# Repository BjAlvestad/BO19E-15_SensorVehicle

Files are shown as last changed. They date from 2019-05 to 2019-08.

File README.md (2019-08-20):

# BO19E-15 Sensor vehicle for use by students in practical application of interdisciplinary skills 

## Table of Contents

* [About the Project](#about-the-project)
  * [Built With](#built-with)
* [Getting Started](#getting-started)
* [Usage](#usage)
* [Contributing](#contributing)
* [License](#license)
* [Acknowledgements](#acknowledgements)

## About The Project
This project was the bachelor thesis of Bjørnar Alvestad, Benjamin Odland Skare and Erlend Lone.
Our goal was to make a learining tool for automation/electrical engineering students at Western Norway University of Applied Science. The physical car we made has ultrasonic sensors and a LiDAR for measuring distance to obstacles and it has encoders that is used to determine the speed of the car and the distance travelled. HVL SensorVehicle Simulator was made so that the students could test their control logics without having the physical car present.

### Built With
**<u>SensorVehicle-main (UWP app, C#, XAML)</u>**
* Extension that makes it easier to create UWP apps [Windows Template Studio](https://marketplace.visualstudio.com/items?itemName=WASTeamAccount.WindowsTemplateStudio)	

* MVVM framework [Prism](https://prismlibrary.github.io/docs/)

**<u>Simulator-2D</u> (UWP app, C#, XAML)**

* Game developement framework [MonoGame](http://www.monogame.net/)

* Simple 2D camera for Monogame [Comora](https://github.com/aloisdeniel/Comora)

* Map editor [Tiled](https://www.mapeditor.org/)

* Importer for Tiled maps [TiledSharp](https://github.com/marshallward/TiledSharp)

**<u>SensorVehicle-extras (UWP app, C#, XAML, JavaScript, CSS, HTML)</u>**

* Starting point for webcam streaming [HttpWebcamLiveStream](https://github.com/SaschaIoT/HttpWebcamLiveStream/tree/master/HttpWebcamLiveStream)

**<u>Android app for remote control (Java - Android Studio)</u>**

**<u>Code for microcontrollers (C++ - Visual Micro)</u>**

## Getting Started
To fully use HVL SensorVehicle Main and write your own control logic you need to: <br>
* **<u>For writing your own control logic:</u>**
```sh
git clone https://github.com/BjAlvestad/BO19E-15_SensorVehicle-Simplified.git
```
* **<u>For access to the entire software:</u>**
```sh
git clone https://github.com/BjAlvestad/BO19E-15_SensorVehicle.git
```
* Install HVL SensorVehicle Simulator from [Microsoft Store](https://www.microsoft.com/en-us/p/hvl-sensorvehicle-simulator/9nbs6gn8sqlg?activetab=pivot:overviewtab)
* Open SensorVehicle-main.sln and navigate to one of the StudentXX.cs-files

## Usage
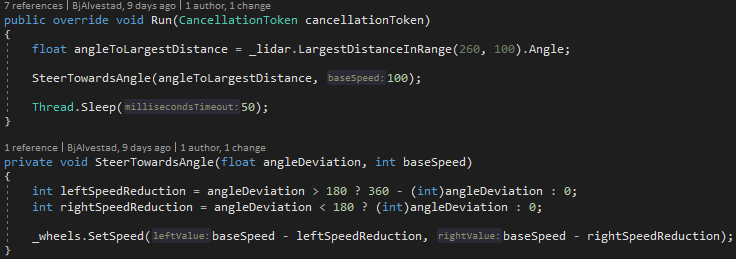
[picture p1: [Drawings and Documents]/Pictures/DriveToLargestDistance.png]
Control logic example
 <br>
The above example shows how one can make the car drive towards the largest distance reported by the LiDAR.

To write your own control logic, navigate to the files in the picture below.
The different StudentXX.cs-files contains instruction where to write the control logic. <br>

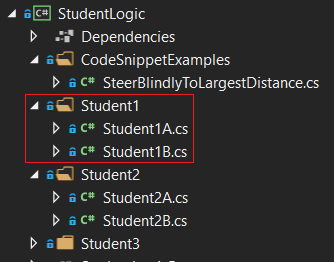
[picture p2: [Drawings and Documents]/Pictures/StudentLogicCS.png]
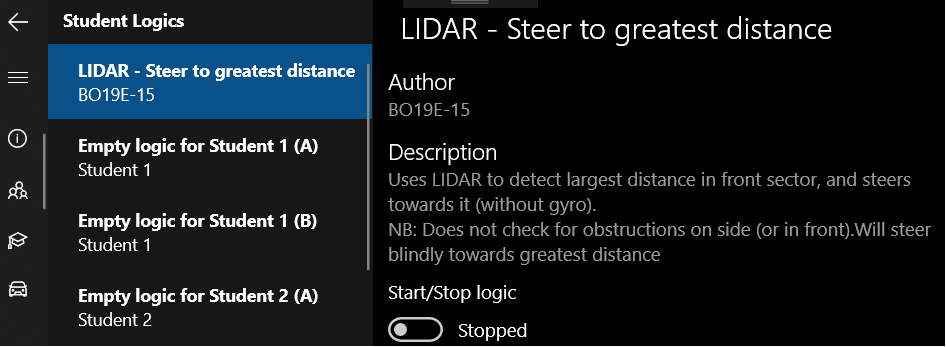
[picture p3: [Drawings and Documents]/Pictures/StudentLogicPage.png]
  <br>
An overview of the different control logics from the shown .cs-files will appear in the student logic page. <br><br>

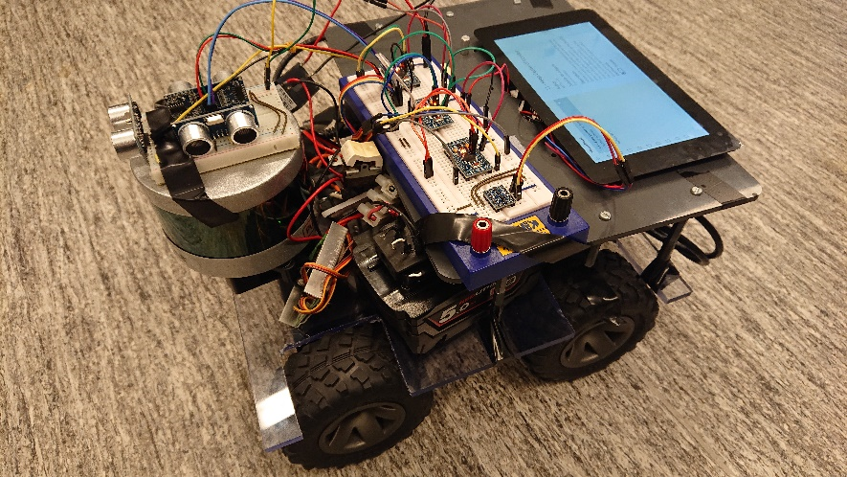
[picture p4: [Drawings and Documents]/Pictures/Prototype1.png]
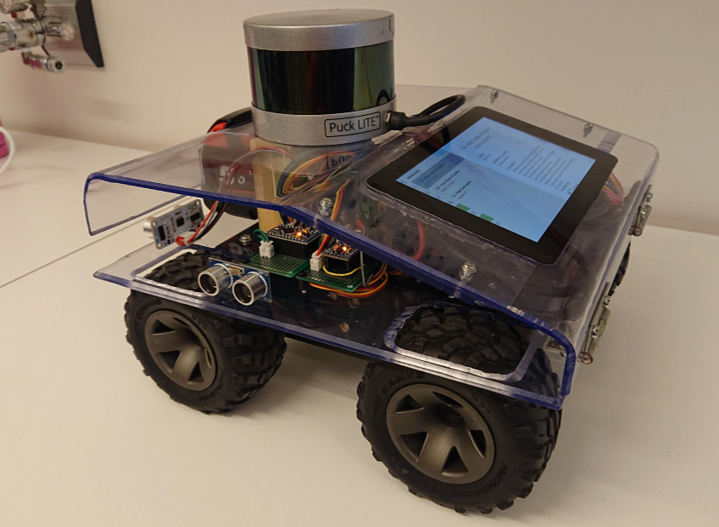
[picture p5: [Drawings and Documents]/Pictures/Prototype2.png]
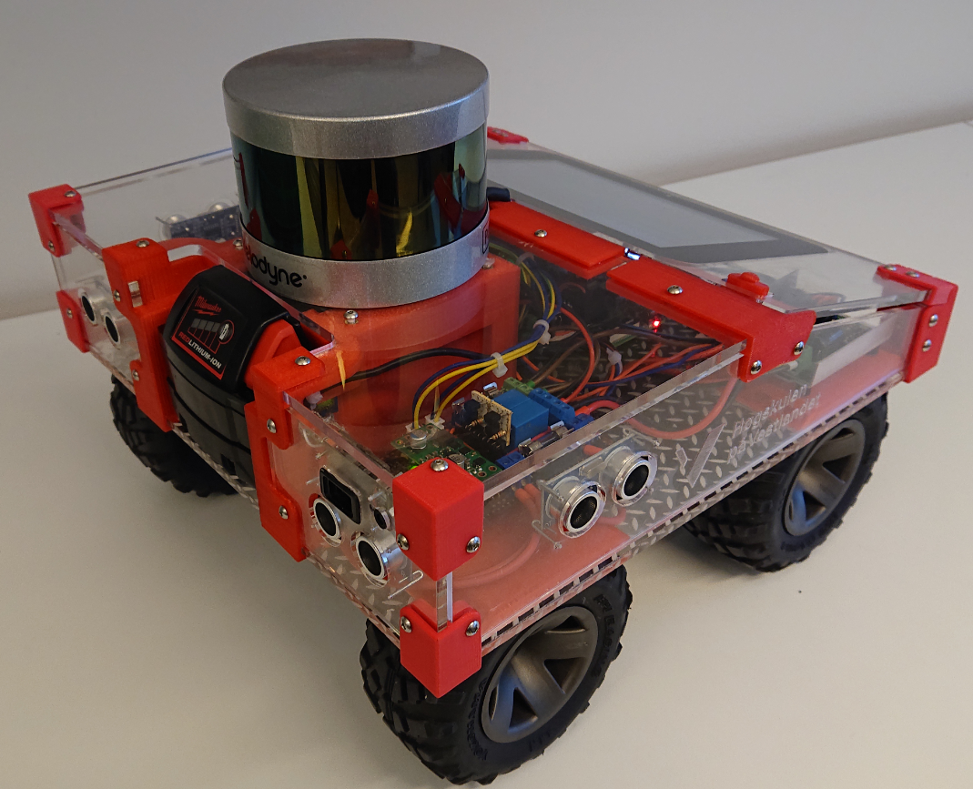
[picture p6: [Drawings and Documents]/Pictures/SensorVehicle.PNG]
         <br><br>
The different version of the car that was made are shown in the pictures above.
The first version was made to get the different hardware components to work.
The second version was made fully functional. The complete software was made by using this version of the sensor vehicle.
The third and final version was made even more solid than the second version. The brackets were 3D-printed and the sheet were cut with laser cutter.

For more information about the development process and a detailed user manual, see [Bachelor thesis document](https://github.com/BjAlvestad/BO19E-15_SensorVehicle/tree/develop/%5BDrawings%20and%20Documents%5D/Bachelor%20Thesis%20(text%20in%20Norwegian)/BO19E-15%20Bacheloropp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) (Norwegian)

## Contributing

Contributions are what make the open source community such an amazing place to be learn, inspire, and create. Any contributions you make are **greatly appreciated**.

1. Fork the Project
2. Create your Feature Branch (`git checkout -b feature/AmazingFeature`)
3. Commit your Changes (`git commit -m 'Add some AmazingFeature`)
4. Push to the Branch (`git push origin feature/AmazingFeature`)
5. Open a Pull Request

## License

Distributed under the MIT License. See `LICENSE` for more information.

## Acknowledgements
* This README is based on [othneildrew's Best-README-Template](https://github.com/othneildrew/Best-README-Template/blob/master/README.md)

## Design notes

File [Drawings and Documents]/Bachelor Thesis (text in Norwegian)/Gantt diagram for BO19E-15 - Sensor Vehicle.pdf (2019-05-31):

12 | 17 | 24 | 31 | 7 | 14 | 21 | 28 | 4 | 11 | 18 | 25 | 4 | 11 | 18 | 25 | 1 | 8 | 15 | 22 | 29 | 6 | 13 | 20 | 27 | 3 | 10
| | Dec '18 | | | Jan '19 | | | | | Feb '19 | | | | Mar '19 | | | | Apr '19 | | | | | May '19 | | | Jun '19
BO19E-15 - Sensor Vehicle ... | 0h | 58%
Møter, presentasjoner og innleveri... | 0h | 63%
Innlevering av forstudie | 0 | 100%
Midtveispresentasjon | 0 | 100%
Bacheloroppgave seminar | 0 | 100%
Innlevering av bacheloroppgave | 0 | 0%
Presentasjon av bacheloroppgave | 0 | 0%
EXPO / avslutningsfest | 0 | 0%
Presentasjon for forkursstudenter | 0 | 100%
Bacheloroppgaveseminar | 0 | 100%
Documentation & Reports | 0h | 23%
Forstudie | 0 | 100%
Brukermanual | 0 | 0%
Bacheloroppgave | 0 | 0%
(hvis tid) Kodeforklaring | 0 | 0%
Hardware & Microcontrollers | 0h | 100%
Analog styring av hjul | 0 | 100%
Avstandsmåling med ultrayd | 0 | 100%
Touch skjerm | 0 | 100%
Power distributer | 0 | 100%
Sensor Vehicle base functions compl... | 0 | 100%
Collision protection | 0 | 90%
(if time) Look into possibility for addi... | 0 | 0%
Main UWP app | 0h | 52%
Sensor input - LIDAR | 0 | 100%
Sensor input - Ultralyd | 0 | 100%
Distance klasse (autoselect from LID... | 0 | 0%
Vehicle control - Klasse for å sette hj... | 0 | 100%
Interface for Eksempel/Student logikk | 0 | 90%
Launch simulator if running on PC | 0 | 100%
AppService Client | 0 | 100%
Improve robustness / code cleanup | 0 | 0%
Rewrite code to Async | 0 | 0%
Simulator | 0h | 72%
Prework on simulator | 0 | 100%
Write or find TiledMap importer/pars... | 0 | 100%
Create class for simulating LIDAR | 0 | 100%
Configure as AppService provider | 0 | 100%
Send LIDAR distance to / receive spe... | 0 | 100%
TEST simulator physics against real ... | 0 | 100%
(if time) Give option to select maps | 0 | 0%
(if time) Create more maps | 0 | 0%
Extras - Streaming | 0h | 89%
Prework on streaming app | 0 | 100%
Add streaming possibility | 0 | 100%
Add layout of UWP app | 0 | 100%
Keep streaming when app is in backg... | 0 | 100%
Add functionality from IoT Dashboard | 0 | 100%
Add possibility to launch main app | 0 | 100%
Remove unused/unnecessary code | 0 | 100%
Finish what is marked TODO in code | 0 | 0%
Extras - Android | 0h | 0%
Example Control Logic / Student ta... | 0h | 0%
Eks. Logikk 01 - Hold midten av kori... | 0 | 100%
Eks. Logikk 02 - Right hand search w/... | 0 | 0%
(if time) Eks. Logikk 03 - Build map | 0 | 0%

Erlend Lone
Benjamin Skare, Bjørnar Alvestad, Erlend Lone Benjamin Skare, Bjørnar Alvestad, Erlend Lone Erlend Lone
Benjamin Skare, Bjørnar Alvestad, Erlend Lone Benjamin Skare, Bjørnar Alvestad, Erlend Lone Benjamin Skare, Bjørnar Alvestad, Erlend Lone Benjamin Skare, Bjørnar Alvestad, Erlend Lone

Benjamin Skare
Benjamin Skare, Erlend Lone Benjamin Skare
Benjamin Skare
Benjamin Skare, Erlend Lone

Bjørnar Alvestad

Bjørnar Alvestad
Bjørnar Alvestad

Bjørnar Alvestad

Bjørnar Alvestad
Bjørnar Alvestad, Erlend Lone Bjørnar Alvestad
Bjørnar Alvestad
Bjørnar Alvestad
Erlend Lone

Erlend Lone

Erlend Lone
Erlend Lone
Erlend Lone
Erlend Lone
Erlend Lone
Erlend Lone
Erlend Lone
Erlend Lone

Powered by TCPDF (www.tcpdf.org)

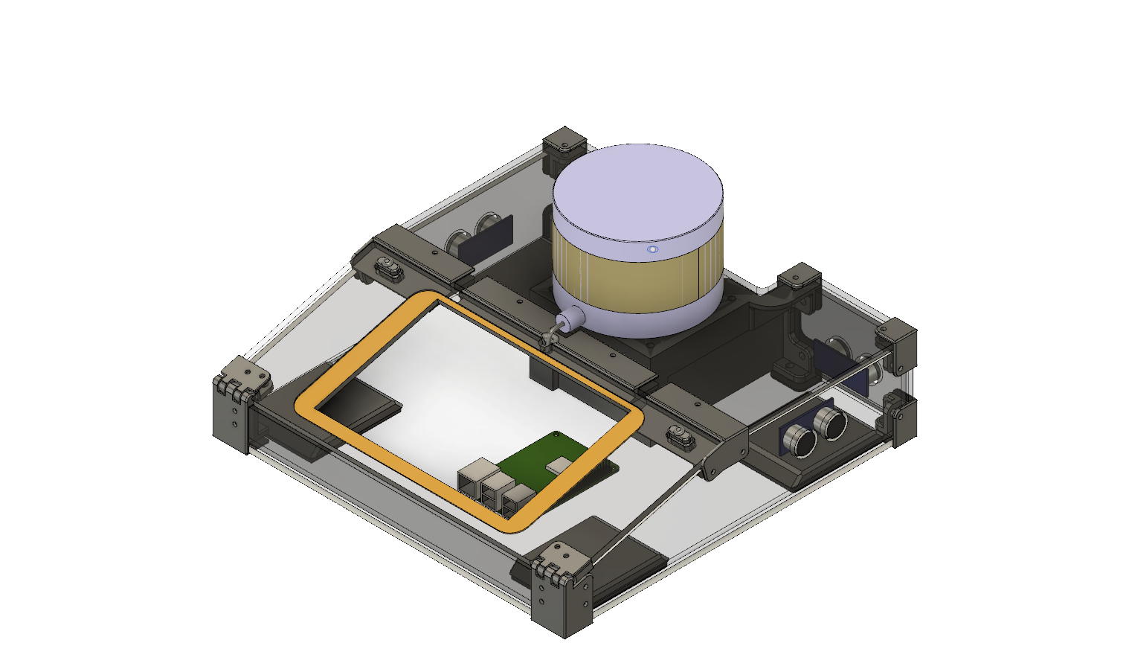
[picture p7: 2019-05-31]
[Drawings and Documents]/Hardware design and components/3D models of vehicle chassis/Chassi v41.1 - Aft right.png

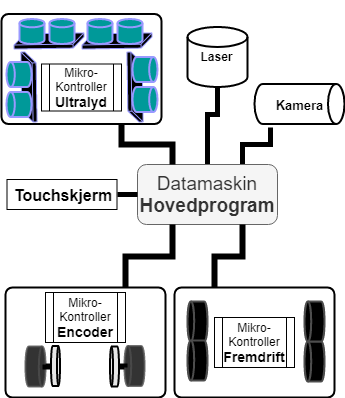
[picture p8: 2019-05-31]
[Drawings and Documents]/System and application drawings/Simplified system schematics (text in Norwegian).png

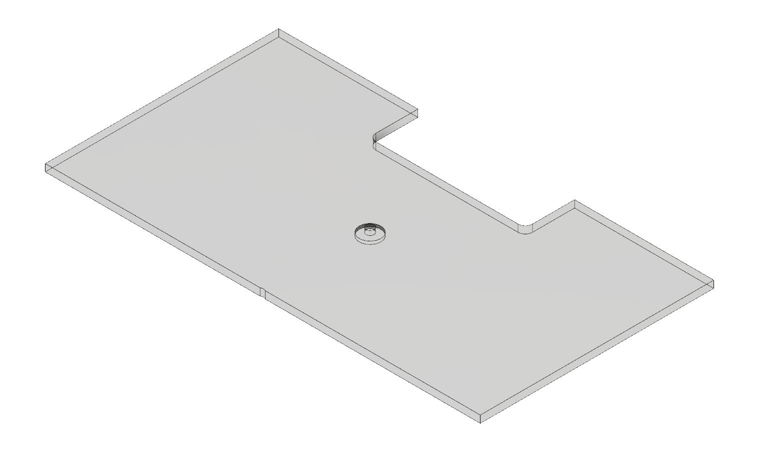
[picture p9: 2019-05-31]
[Drawings and Documents]/Hardware design and components/3D models of vehicle chassis/Plates/Topp v18.png

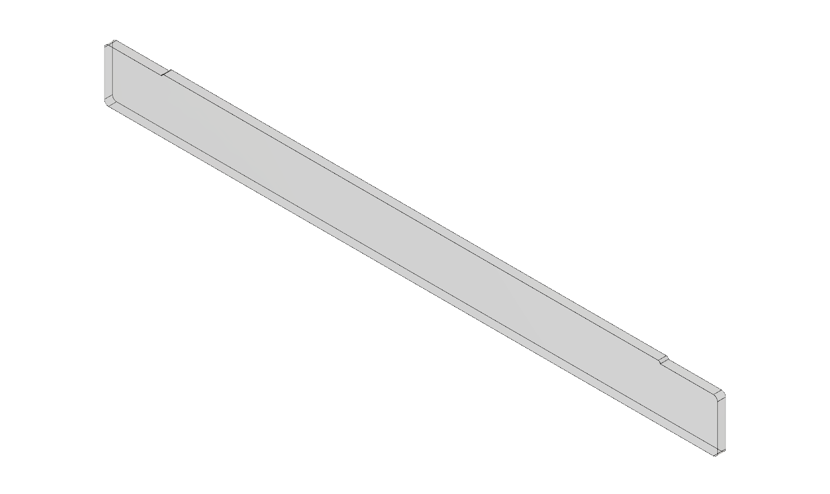
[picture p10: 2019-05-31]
[Drawings and Documents]/Hardware design and components/3D models of vehicle chassis/Plates/Bak v17.png

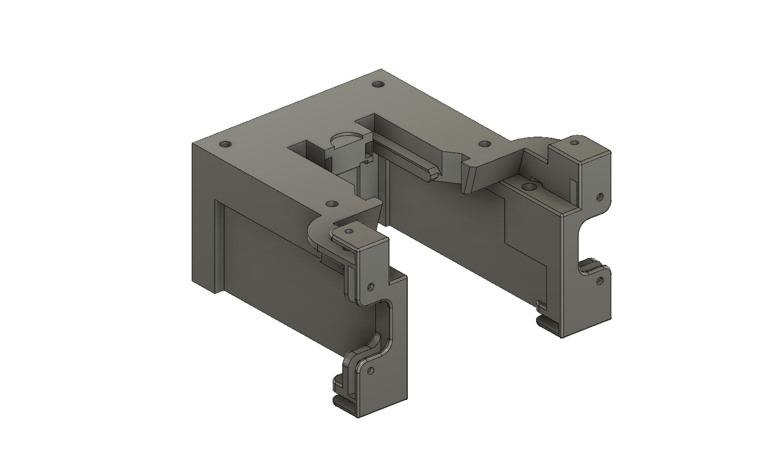
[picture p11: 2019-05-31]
[Drawings and Documents]/Hardware design and components/3D models of vehicle chassis/Brackets/Batteriholder3 v33.png

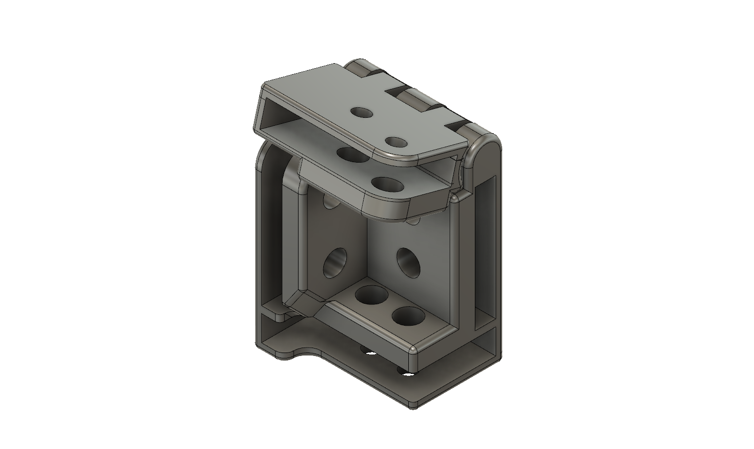
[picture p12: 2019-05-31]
[Drawings and Documents]/Hardware design and components/3D models of vehicle chassis/Brackets/Brakett BV v45.png

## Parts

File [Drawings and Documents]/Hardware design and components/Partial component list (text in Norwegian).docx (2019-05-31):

###### A.1 Komponentliste

###### A.1.1 Ettkortsdatamaskin

7" universal LCD | m/touch
HDMI kabel | HMDI til mini-HDMI
USB kabel | Mini til type A
Raspberry Pi 3B
Kjøleribber | m/vifte
DC-regulator | 5 til 3,3 volt
Logic level coverter | I2C
Koblingspunkt

###### A.1.2 Sensorer og moduler

Motordriver | Sabertooth 2X12 RC
Ultrasonic sensor | HC-SR04 | 4 stk
Velodyne Lidar VLP-16 | m/koblingsboks, bolt(tomme)
Nettverkskabel | Cat 5, RJ-45
Webkamera | Microsoft LifeCam HD-3000
Batteri m/lader | Milwaukee M18™ 5.0 AH | 2 stk
DC-motor m/gir | (2 stk med enkoder) | 4 stk
Gyro | Bosch BNO055 9-Axis IMU | 2 stk (ikke på bil)
Gyro | MPU 9250 SPI/IIC 9-Axis | 2 stk (ikke på bil)

###### A.1.3 Strømstyring til Arduino og RPI:

NPN transistor | 2N3906
PNP transistor | 2N3904
Motstand | 100 k ohm
Motstand | 10 k ohm | 2 stk
Koblingspinner

###### A.1.4 «Arduino-kort»:

Arduino Pro-Mini | ATmega328P | 4 stk
I2C buffer IC | TCA4311A | 4 stk
Motstand | 100 k ohm
Motstand | 10 k ohm
Mikrobryter | | 2 stk
Lysdioder
Kontakter
Kretskort
Koblingspunkt

###### A.1.5 Strømforsyning:

Rele | | 4 stk
Sikring | | 4 stk
Sikring
Sikring
5 VDC regulator
Kontakter
Kretskort
Koblingspunkt

###### A.1.6 Festemidler og resten:

Skruer Hex | | 4 stk
Skruer nedsenket | | 4 stk
Avstandsstykker | Plast m/skruer
Gjenger
Plexiglass
Plast
Lydisolasjonsmatte
Ledning
Niter
Ledninger
Kontakter
Strips
Superlim
Stifter dykkert

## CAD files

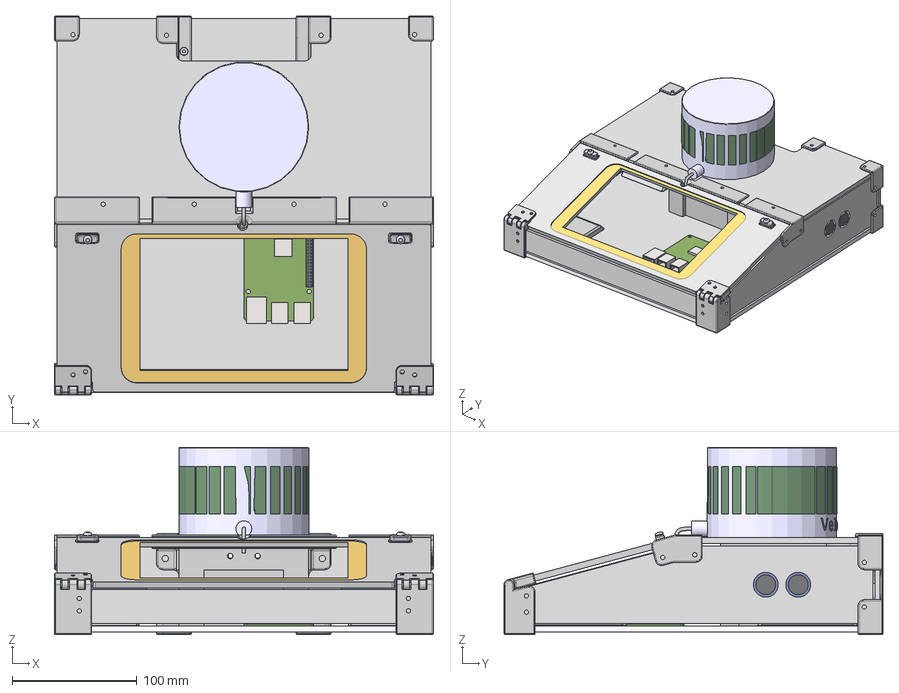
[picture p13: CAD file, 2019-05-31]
[Drawings and Documents]/Hardware design and components/3D models of vehicle chassis/Chassi v41.step
304.3 x 304.0 x 150.1 mm
Bunnplate
Brakett FV x 2
Brakett FV v4(Mirror) x 2
Topp
Side x 2
hjulskjerm x 4
Batteriholder3
Velodyne2
Raspi3B+_Mock
Skjemplate
Bak
SkjermFeste
Ultrasonic x 4
Kamera
Bryter
Component3(Mirror)
Component4(Mirror)

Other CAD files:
[Drawings and Documents]/Hardware design and components/3D models of vehicle chassis/Brackets/Batteriholder3 v33.f3d
[Drawings and Documents]/Hardware design and components/3D models of vehicle chassis/Brackets/Brakett BV v45.f3d
[Drawings and Documents]/Hardware design and components/3D models of vehicle chassis/Brackets/Brakett FV v8.f3d
[Drawings and Documents]/Hardware design and components/3D models of vehicle chassis/Brackets/SkjermFeste v22.f3d
[Drawings and Documents]/Hardware design and components/3D models of vehicle chassis/Brackets/hjulskjerm v9.f3d
[Drawings and Documents]/Hardware design and components/3D models of vehicle chassis/Components/Bryter v2.f3d
[Drawings and Documents]/Hardware design and components/3D models of vehicle chassis/Components/Kamera v2.f3d
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

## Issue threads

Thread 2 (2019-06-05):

Standardise all sensors to report distances in meters (encoder is currently in cm)

BjAlvestad, 2019-06-05:
In the main program, the public properties in Encoder classes exposes distance values as centimeters, while the other sensors utilizes meters.
This may cause confustion for the people writing control logics for the vehicle.

Two alternative options that would fix the issue:

**Option 1**:
- Add aditional metod reporting distance in meters (in addition to cm).
This would mean an increment of the minor version (new functionality but no breaking change).

**Option 2**
- Change methods in main program to utilize values as meters instead of centimeters.
- Modify the Encoder page and overview page to also reflect these changes (the displayed units).
This would mean an increment of the major version (breaking change for code allready using data from the encoders).

PS:
The microcontroller should still transfere the distance as centimeters and a whole number.
The change should only be carried out in the main program (dividing the received distance by 100).

PPS:
The versioning refered to above in the two options is based on [Semantic Versioning 2.0.0](https://semver.org/)

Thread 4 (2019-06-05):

Rewrite code to utlilize async/await fully in the SensorVehicle-main app (requires async I2c library) - responsive UI

BjAlvestad, 2019-06-05:
There is a mix of async and synchronous code in the SensorVehicle-main application.
Async/await should be used "from bottom to top".

When the code is running on a PC (against the simulator), the implementation for IVehichleCommunication that is used is "SimulatedVehicleCommunication". This utilizes an AppService to communicate with the simulator, which only offers async methods.

When the code is running on the physical car, the implementation for IVehicleCommunication is "VehicleCommunication" which utilizes the UWP I2c library. This offers only synchronous methods. Async is not an option here.

For this reason, we have been forced to mix async and non-async code.

### The way we have solved this:
Inside "SimulatedVehicleCommunication"-class:

**When sending data to simulator** (setting wheel speed) we send without awaiting the task.
Problem caused by this: any exceptions that occurs behind this method will be swallowed since we are not awaiting them.

**When requesting data from simulator** we force the method to run synchronously by adding ".GetAwaiter().GetResult();" to the async method.
Potential problem: may cause code to deadlock, however this has not occured while we have been testing the code.

### Better way of fixing issue - if async I2C library can be found
If Microsoft releases an async version of the I2C library, then it would be better to rewrite all the code to async, since this would also ensure that the GUI remains responsive.
(If I2c communication fails there will be approximately a seconds delay before an exception is thrown. If the update was initiated from the GUI, this will cause a momentary UI freeze).

PS: This suggestion for fix is only relevant if an async I2c library can be found.

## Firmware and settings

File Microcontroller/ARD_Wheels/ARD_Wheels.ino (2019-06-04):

// Code for SensorVehicle v.1.0
// BO19E-15


// Communication
#include <Wire.h>
const int pin_I2C_enable = 14;
const int address = 0x20;
const int size_of_byte_array = 23;
void receive_event(int x);
void assemble_ints_from_byte_array(long number_of_longs, int start_index, byte array[]);
void assemble_data_from_vehicle(byte vehicle_byte_array[]);

// PWM
#include <Servo.h>
Servo wheels_right;
Servo wheels_left;

const int pin_pwm_right = 7;
const int pin_pwm_left = 6;
const int pin_mode_1 = 11;
const int pin_mode_2 = 10;
const int pin_relay_sabertooth = 9;
const int pin_mode_switch = 12;

const int data_standstill = 0;
const int data_full_reverse = -100;
const int data_full_forward = 100;
const int pwm_start_reverse = 1330;
const int pwm_full_reverse = 1130; // 12 v (1000)
const int pwm_start_forward = 1600;
const int pwm_full_forward = 1840;  // 12 v (2000)
const int pwm_standstill = 1500;
const int ramp_up = 20;

int data_left, data_right;
int speed_left, speed_right;
int speed_map(int data);

// Safety mode
int mode = 2;  // 3 = full speed, 0 = stop
int data_check(int data);
int mode_check(int data);

void setup()
{
	Wire.begin(address);

	pinMode(pin_mode_1, INPUT_PULLUP);
	pinMode(pin_mode_2, INPUT_PULLUP);
	pinMode(pin_relay_sabertooth, OUTPUT);
	pinMode(pin_mode_switch, INPUT_PULLUP);
	pinMode(LED_BUILTIN, OUTPUT);

	digitalWrite(pin_relay_sabertooth, LOW);

	wheels_right.attach(pin_pwm_right);
	wheels_left.attach(pin_pwm_left);
	wheels_left.writeMicroseconds(pwm_standstill);
	wheels_right.writeMicroseconds(pwm_standstill);
	Wire.onReceive(receive_event);

	data_left = data_standstill;
	data_right = data_standstill;
	speed_left = pwm_standstill;
	speed_right = pwm_standstill;

	pinMode(pin_I2C_enable, OUTPUT);
	digitalWrite(pin_I2C_enable, HIGH);
}

void loop()
{
	if (data_left==0 && data_right == 0)
	{
		digitalWrite(pin_relay_sabertooth, LOW);
	}
	else
	{
		digitalWrite(pin_relay_sabertooth, HIGH);
	}

	speed_left = speed_map(mode_check(data_left));
	speed_right = speed_map(mode_check(data_right));
	
	wheels_right.writeMicroseconds(speed_right);
	wheels_left.writeMicroseconds(speed_left);

	/*String s = "Ld: = " + String(data_left) + "\t Rd: " + String(data_right) +
		"\t L: " + String(speed_left) + "\t R: " + String(speed_right) +
		"\t MODE: " + mode +
		"\t SWITCH: " + digitalRead(pin_mode_switch);
	Serial.println(s);
	delay(1000);*/
}

void receive_event(int x)
{
	byte data[size_of_byte_array];
	
	if (Wire.available())
	{
		for (int i = 0; i < size_of_byte_array; i++)
		{
			data[i] = Wire.read();
		}
		assemble_data_from_vehicle(data);
	}
}

int speed_map(int data)
{
	if (data > 0)
	{
		data = map(data, data_standstill, data_full_forward, pwm_start_forward, pwm_full_forward);
		return data;
	}
	else if (data < 0)
	{
		data = map(data, data_standstill, data_full_reverse, pwm_start_reverse, pwm_full_reverse);
		return data;
	}
	else
	{
		return pwm_standstill;
	}
}

int data_check(const int data)
{
	if (data < data_full_reverse)
	{
		return  data_full_reverse;
	}
	else if (data > data_full_forward)
	{
		return data_full_forward;
	}
	else
	{
		return data;
	}
}

int mode_check(int data)
{
	if (digitalRead(pin_mode_switch))
	{
		digitalWrite(LED_BUILTIN, HIGH);
		mode = 2;
		return (2 * data) / 3;
	}
	digitalWrite(LED_BUILTIN, LOW);

	if (!digitalRead(pin_mode_1) && !digitalRead(pin_mode_2) )
	{
		mode = 0;
		return 0;
	}
	else if (!digitalRead(pin_mode_1) && digitalRead(pin_mode_2))
	{
		mode = 1;
		data = data / 2;
		return data;
	}
	else if (digitalRead(pin_mode_1) && !digitalRead(pin_mode_2))
	{
		mode = 2;
		data = (2 * data) / 3 ;
		return data;
	}
	else if (digitalRead(pin_mode_1) && digitalRead(pin_mode_2))
	{
		mode = 3;
		return data;
	}
	return 0;
}

void assemble_data_from_vehicle(byte vehicle_byte_array[])
{
	int address = vehicle_byte_array[0];
	int code = vehicle_byte_array[1];
	const int number_of_longs = vehicle_byte_array[2];
	const int empty_bytes = 3;
	assemble_ints_from_byte_array(number_of_longs, empty_bytes, vehicle_byte_array);
}

void assemble_ints_from_byte_array(const long number_of_longs, const int start_index, byte array[])
{
	if (size_of_byte_array >= (sizeof(long)*number_of_longs + start_index))
	{
		const int bits_in_long = sizeof(long) * 8;
		long longs[2];

		for (int i = 0; i < number_of_longs; i++)
		{
			int assembled_long = 0;
			const int shift_by_long = sizeof(long) * i;

			for (int j = 1; j <= sizeof(long); j++)
			{
				assembled_long |= array[start_index - 1 + j + shift_by_long] << (bits_in_long - 8 * j);
			}
			longs[i] = assembled_long;
		}

		data_left = data_check(longs[0]);  // Between -100 and 100;
		data_right = data_check(longs[1]);
	}
}

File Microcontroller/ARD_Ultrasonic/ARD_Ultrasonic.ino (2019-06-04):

// Code for SensorVehicle v.1.0
// BO19E-15

// https://create.arduino.cc/projecthub/MisterBotBreak/how-to-use-an-ultrasonic-sensor-181cee

// Communication
#include <Wire.h>
const int i2c_enable_pin = 15;  //A1
const int pin_new_message = 10;
const int size_of_byte_array = 23;
const byte address = 0x25;
void i2c_request();
void send_byte_array(int message, int array_length, long longs_to_be_sent[]);

// Ultrasonic
const int pin_trig_left = 5;
const int pin_echo_left = 4;
const int pin_trig_right = 7; 
const int pin_echo_right = 6; 
const int pin_trig_forward_left = 3;
const int pin_echo_forward_left = 2;
const int pin_trig_forward_right =9; 
const int pin_echo_forward_right =8; 
long ultrasonic(int trig_pin, int echo_pin);

// Defines variables
long distance_left;
long distance_right;
long distance_forward_left;
long distance_forward_right;
const int pause = 30;

// Safety mode
const int pin_mode_1 = 12;
const int pin_mode_2 = 11;
const int pin_mode_switch = 14;
const int safe_distance_reduce = 5;
void check_distance(long distance);
void set_mode(int i);
int count;
int mode;


void setup() {
	pinMode(pin_trig_left, OUTPUT);
	pinMode(pin_echo_left, INPUT);

	pinMode(pin_trig_right, OUTPUT);
	pinMode(pin_echo_right, INPUT);

	pinMode(pin_trig_forward_left, OUTPUT);
	pinMode(pin_echo_forward_left, INPUT);

	pinMode(pin_trig_forward_right, OUTPUT);
	pinMode(pin_echo_forward_right, INPUT);

	pinMode(pin_mode_1, OUTPUT);
	pinMode(pin_mode_2, OUTPUT);

	digitalWrite(pin_mode_1, HIGH);
	digitalWrite(pin_mode_2, LOW);

	pinMode(pin_new_message, OUTPUT);
	digitalWrite(pin_new_message, LOW);

	Wire.begin(address);
	Wire.onRequest(i2c_request);

	mode = 1;

	pinMode(pin_mode_switch, INPUT_PULLUP);
	pinMode(LED_BUILTIN, OUTPUT);

	pinMode(i2c_enable_pin, OUTPUT);
	digitalWrite(i2c_enable_pin, HIGH);
}

void loop() {
	count = 0;

	delay(4); // hack

	distance_forward_right = ultrasonic(pin_trig_forward_right, pin_echo_forward_right);
	check_distance(distance_forward_right);
	delay(pause);

	distance_left = ultrasonic(pin_trig_left, pin_echo_left);
	check_distance(distance_left + 5);
	delay(pause);

	distance_forward_left = ultrasonic(pin_trig_forward_left, pin_echo_forward_left);
	check_distance(distance_forward_left);
	delay(pause);

	distance_right = ultrasonic(pin_trig_right, pin_echo_right);
	check_distance(distance_right + 5);
	delay(pause);

	digitalWrite(pin_new_message, HIGH);


	/*const String text = "L: " + String(distance_left) + "\t FL: " +String(distance_forward_left) + "\t FR: " +
		String(distance_forward_right) + "\t R: " + String(distance_right) + "\t Mode: " + String(mode) + "\t Count: " + String(count);
	Serial.println(text);*/

	if (count > 3)
	{
		if (mode < 3)
		{
			mode++;
		}
		set_mode(mode);
	}
}

void i2c_request() {
	long longs_to_be_sent[] = { distance_left, distance_forward_right, distance_right, distance_forward_left  };
	const int array_length = sizeof(longs_to_be_sent) / sizeof(long);
	send_byte_array(0, array_length, longs_to_be_sent);

	digitalWrite(pin_new_message, LOW);
}

long ultrasonic(const int trig_pin, const int echo_pin)
{
	digitalWrite(trig_pin, LOW);
	delayMicroseconds(2);
	digitalWrite(trig_pin, HIGH);		// Sets the trigPin on HIGH state for 10 micro seconds
	delayMicroseconds(10);
	digitalWrite(trig_pin, LOW);
	const long duration = pulseIn(echo_pin, HIGH, 24000);  // Reads the echoPin, returns the sound wave travel time in microseconds

	const int distance = duration * 0.034 / 2;

	if (distance > 400)
	{
		return 400;
	}
	else if (distance == 0)
	{
		return 401;
	}
	else
	{
		return distance;
	}
}

void check_distance(const long distance)
{
	auto reduced_safety = 0;

	if (digitalRead(pin_mode_switch) == HIGH)
	{
		reduced_safety = safe_distance_reduce;
		digitalWrite(LED_BUILTIN, HIGH);
	}
	else
	{
		digitalWrite(LED_BUILTIN, LOW);
	}

	if (distance < 14 - reduced_safety)
	{
		mode = 0;
		set_mode(mode);
	}
	else if (distance < 17 - reduced_safety)
	{
		if (mode < 1)
		{
			count++;
		}
		else
		{
			mode = 1;
			set_mode(mode);
		}
	}
	else if (distance < 20 - reduced_safety)
	{
		if (mode < 2)
		{
			count++;
		}
		else
		{
			mode = 2;
			set_mode(mode);
		}
	}
	else
	{
		if (mode < 3)
		{
			count++;
		}
	}
}

void set_mode(const int i)
{
	switch (i)
	{
	case 0:
		digitalWrite(pin_mode_1, LOW);
		digitalWrite(pin_mode_2, LOW);
		break;
	case 1:
		digitalWrite(pin_mode_1, LOW);
		digitalWrite(pin_mode_2, HIGH);
		break;
	case 2:
		digitalWrite(pin_mode_1, HIGH);
		digitalWrite(pin_mode_2, LOW);
		break;
	case 3:
		digitalWrite(pin_mode_1, HIGH);
		digitalWrite(pin_mode_2, HIGH);
		break;
	default:
		break;
	}
}

void send_byte_array(const int message, const int array_length, long longs_to_be_sent[])
{
	byte byte_array[size_of_byte_array];
	byte_array[0] = byte(address);
	byte_array[1] = byte(message);
	byte_array[2] = byte(array_length);
	const int elements_before_long = 3;

	const int bit_size_of_long = sizeof(long) * 8;

	for (int i = 0; i < array_length; i++)
	{
		const int shift_by_long = sizeof(long) * i;
		for (int j = 1; j <= sizeof(long); j++)
		{
			byte_array[(elements_before_long - 1) + shift_by_long + j] = byte(longs_to_be_sent[i] >> (bit_size_of_long - 8 * j));
		}
	}
	Wire.write(byte_array, size_of_byte_array);
}

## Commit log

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2018-12-23 Adds event handler for launch via protocol
    **Note that the event handler does not yet contain the code required to launch**.
    The code needed to do that could be similar to the code i OnLaunched().
    At its current state, the app can be launched from a different app by creating and calling an async method containing the following code:
    <
    var uri = new Uri("hvl-sensorvehicle-simulator:"); // launch arguments may be put behind the colon
    var success = await Windows.System.Launcher.LaunchUriAsync(uri)
    >
    But currently the simulator app will never load properly, since the loading code is missing from the event handler
    (See suggestion in reply on: https://social.msdn.microsoft.com/Forums/sqlse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
2018-12-23 Fixes car turning round when wheelspeeds were zero
    Checks if wheelspeeds are equal, and if so, does not calculate angularVelocity.
    It will stay at 0, which is what it gets initialized at.
    Note:
    This commit just fixes a glaring bug (car turning arround on the spot, when it should stand still).
    The Drive2() methot is still not fully tested, nor fully developed.
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2019-01-17 Removes Monogame.Extended (Tiled map importer)
    Monogame extended was used for importing maps.
    However the API documentation was poor / severely lacking. And it was ovely complicated requiring a dll refrence in the content pipeline tool, which for UWP apps is kept in the user folder. This was causing issues for people pulling the code to other computers.
    Monogame.Extended are currently working on a 2.0 release which is supposed to improve the API significanly, but we do not have time to wait for that, and since we only use it for importing maps we have decided to go for a more specialized library for parsing Tiled maps instead.
    Monogame.Extended is removed and will be replaced by TiledSharp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
2019-01-18 Adds code for drawing a map using TiledSharp
    TiledSharp does not have build in code for drawing the map, only for parsing the TMX file to an object.
    This code makes the assumption that the maps will be created with the floor layer at the bottom, and then the wall layer above that.
    There is currently an issue with scaling that for some values the map will get visible grid lines (see comments in LoadContent() method inside SimulatorGame.cs for more details).
    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
2019-01-20 Changes LidarDistance class to implement IDistance
    Adds missing fields for MinRange, MaxRange and Resolution, and sets them in constructor according to values stated in manual.
    (See VLP-16 user manual page 3 and 10 where it is stated a minimum range of 1 meter and maximum of 100 meter).
    The Resolution was set to float.NaN since it is unknown.
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2019-01-20 Adds test code for Lidar in Console Test App
    This project is intended for testing parts of the VehicleEquipment library.
    This commit contains some early version of tests for LidarDistance class and LidarDistanceCollector.
    (And also adds a refrence to the VehicleEquipment library).
    Testing the LidarDistance class would also test all the classes below, such as LidarDistanceCollector, LidarPacketInterpreter, LidarPacketReceiver etc.
    The purpose of also testing the lower classes seperately (e.g. LidarDistanceCollecor) is to narrow down on the root cause, if the upper class exibits any issues.
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2019-01-27 Refactoring / change in how Lidar classes work
    Summary:
    Changes from packet collecting in separate thread and event to create loose coupling.
    Changes to async packet collecting (single thread) and uses DI (interface passed as argument to LidarDistance constructor) to create loose coupling.
    Changes TO - details:
    LidarDistance now utelizes an async method in a sort-of 'fire-and-forget' way, where it utilises its packetReceiver (which LidarDistance gets as an ILidarPacketReceiver argument in the constructor) to collect packets, and then uses the static LidarPacketInterpreter to interpret the packets.
    The Distance will periodically update via the use of the async method.
    NOTE:
    further investiga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
2019-02-09 Changes ultrasonic interface and model
    Ultrasonic inherits from BindableBase (for simplified propery changed notifications).
    Removes the DistanceLeft() etc. methods and replaces them with properties.
    Changes logic so that each request does not try to read from microcontroller, but will instead only get new data from the microcontroller if the last reading is older than the selected "PermissableDistanceAge".
    The check and update of the distances is done in the UpdateDistanceProperties() method.
    The UpdateDistanceProperties() method contains a lock, in case two threads thould attempt to update at the same time. Once the first thread has updated the fields, the second thread will immediately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
2019-02-11 Removes BindableBase from ultrasonic
    Since the model will be changed by multiple threads, and since property changed notification won't allways be neseccary (and may make the control logic run slower), the Ultrasonic class has been changed back to POCO.
    The Prism.Core nuget package has also been removed from the VehicleEquipment project.
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2019-02-13 Changes package version from 6.2.3 to 6.1.9
    Reduces package version of Microsoft.NETCore.UniversalWindowsPlatform from 6.2.3 to 6.1.9 in Communication library (6.1.9 is the highest available version in the Application project (main UWP project)).
    Prior to this change we were getting the following error once the program was starting on the IoT device:
    ***
    system.typeloadexception: 'could not load type 'system.runtime.compilerservices.iasyncstatemachine' from assembly 'System.Runtime, Version=4.2.1.0, Culture=neutral, ...
    ***
    This occured when trying to await async methods in the VehicleCommunication classes SetUpCommunication() method.
    Reducing the package version to correspond with the ma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
2019-02-21 Fixes issue with slider reset when navigating away
    Previously a new collection was returned (asynchronously) every time the page was entered.
    This caused the sliter to reset, although a thread was still running.
    Activating the slider again would cause a new thread to start running the same logich which is allready running (two logics trying to control at the same time).
    Now the ExampleLogics collection in initialized only once, when the page is first accessed.
    (Note that with these changes, this is no longer done asynchronously).
    This means the slider stays put, and can therefore be stopped even after having navigated away from and back to the page.
    It is no longer possible to run several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
2019-02-21 Locks selected logic if the logic is running
    Prevents user from changing selected logic, if a the currently selected logic is set to run.
    (Note that moving to a different ViewModel and back again will reset view to first in list, bypassing this block, even if the control logic is running, and will only lock again once the user has navigated to the page with the running control logic)
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2019-02-22 Fixes bug causing multiple ExampleLogic threads
    When exiting and entering the ExampleLogic view, while a control logic was set to running, the RunExampleLogic was called again with the same value as before (true).
    This caused the if-test to pass, and a new thread was started.
    Bug was fixed by returning immediately if the value has not changed since last set-request.
    Only one thread is now running, even when exiting and re-entering the page.
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2019-02-22 Adds ErrorMessage property with PropertyChanged
    The PropertyChanged implementation resides in the ThreadSafeNotifyPropertyChanged class we inherit from.
    This enables us to set the ErrorMessage property from inside the ControlLogic thread, and still raise the property changed on the UI thread.
    Also adds a textblock in the view which is bound up against this property.
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2019-02-24 Makes Ultrasound-model raise selective INPC
    Makes IUltrasound interface extend INotifyPropertyChanged, and Ultrasounc class inherit from Helper-class ThreadSafeNotifyPropertyChanged (which in turn implements INotifyPropertyChanged).
    This allows the Ultrasound model to raise property changed notifications.
    This way the View can bind directly to the properties (by exposing the model in the ViewModel). However it will only raise the property changed event for the distance properties IF we set the RaiseNotificationForSelective to true, so that the ControlLogic doesn't raise many notifications when we aren't looking at a view where we actually observe those values.
2019-02-24 Changes ViewModel to leverage the INCP in Model
    The RaisePropertyChanged no longer gets raised at intervals in the ViewModel, but rather the Model will raise PropertyChanged when there has actually occured a change (and selector bool is true).
    The selector bool gets set to true automatically when entering the view (if Power is on), and will be set to false again upon leaving view.
2019-02-25 Implements PropertyChangedNotification on Power
    Makes IPower extend INotifyPropertyChanged so that bindings will update, even if we are refrencing the Interface (instead of casting to base type).
    Implements the interface in MockPower class by inheriting from ThreadSafeNotifyPropertyChanged.
    Changes Power class to also inherit from ThreadSafeNotifyPropertyChanged (in Helpers project), instead of implementing INPC directly in the Power class.
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2019-02-25 Adds exception handling to Ultrasonic sensor
    Any exception that occures while trying to collect data gets stored as a string in a Message Property.
    This gets displayed in a textblock on the Ultrasonic View.
    Tapping the textbox clears the message and error.
    It will not try to collect new values until error has been acknowledged (returns NaN for all distances).
2019-02-25 Adds Boolean to Color converter
    This can be used to set Shell button colors by binding to boolean properties.
    Usage example in XAML (where backgrond gets set to green if Power.Ultrasound is true):
    Background="{x:Bind ViewModel.Power.Ultrasound, Mode=OneWay, Converter={StaticResource BooleanToColorConverter}, ConverterParameter=LimeGreen }
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2019-02-25 Adds store/clear error capabilities in Lidar model
    Adds boolean property for keeping track if there is an unacknowledged alarm active.
    'CollercorMessage' gets renamed to more general 'Message'.
    Adds method for acknowledging/clearing message.
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2019-02-25 Adds a starting point for the Lidar View
    The buttons are connected, and visibility setings bound up.
    TODO:
    Add the missing textboxes/block/lists in the LidarView for settings and sensor data.
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2019-02-27 Makes data from MockLidar dynamic
    Instead of utilizing a fixed data packet, it now generates packets by using the Helper "LidarFormatPacketGenerator".
    The horizontal angles generated will have gradually increasing distances.
    Also the different vertical angles will have different distance values.
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2019-02-27 Adds BUG comment reminder in GetDistancecInRange()
    Noticed issue when we had no valid values in left sector of lidar.
    If perfroming a calculation that spanns zero (i.e. Fwd), it will return List with only a float.NaN, even if there are valid values on the right hand side.
    To be fixed later when improving the calculation logic.
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2019-03-04 Adds error message properties and methods
    The HasUnacknowledgedError property will be used used for putting a red frame arround the shell button when an error is active, and from preventing re-start of control logic until error has been acknowledged.
    ClearMessgage() method will be used for removing the message stored in ErrorMessage property, and to allow the control logic to be started again.
2019-03-04 Adds error message box for Wheel class
    The message box on the WheelsPage is used for displaying error messages from exceptions to the user.
    It can be acknowledged/cleared by tapping the message.
    The wheel class utilises:
    - String property "Message" for storing the error message.
    - ClearMeassage() method for clearing the message and setting HasUnacknowlededError proerty to false.
    - Boolean HasUnacknowlededError property for keeping track of wheter an error is active or not (blocks sending new wheelspeed if true).
2019-03-04 Adds error message box for Power class
    The message box on the PowerPage is used for displaying error messages from exceptions to the user.
    The Power class utilises:
    - Boolean HasUnacknowlededError property for keeping track of whether an error is active or not (blocks switching power state if true).
    Exception handling for state-switcing has just been added for the Lidar as of this commit (TODO comment added).
    Exception handling for opening of pin has been added for all (v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
2019-03-04 Adds shell-button colors/visibility based on state
    If an example logic is running, or a sensor is powered on, the respective shell-button will turn green.
    If it has an error, it will get e red frame.
    In addition, if an example logic is running, the shell button for student logic will be hidden.
    (Student Logic is not yet implemented, but once it is it will also hide the Example Logic if a Student Logic is running).
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2019-03-07 Sets up Encoder (mock)simulation on simulator side
    Currently it doesn't return the distance traveled as it is supposed to, but rather returns the speed at that spesiffic moment in time. A TODO comment has been added in the project as a reminder to be rectified when we have time.
    (EncoderRight has not been tested, since this is not implemented in the main program, nor on physical hardware yet).
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2019-03-08 Fills Lidar distance list with NaN in constructor
    This is to prevent issue with reading from list before the first Lidar measurement.
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2019-03-15 Changes grid definitions for Lidar view
    Changes from fixed margins between the three section to instead have 0.1* (take remaining available space).
    The middle section must have * (not Auto) to prevent the power buttons being pushed off-screen, if there is to littel space (like it is now, middle section will disapear instead).
    Also sets a minimum height for the bottom row (the error message row).
2019-03-15 Makes Lidar settings more narrow, and scrollable
    Reduces the width (and increases height) by adding more line breaks in describtions (the TextBlocks).
    Also puts the entire stackpanel in row0 colum0 inside a ScrollViewer (so that if the data does not fit on the screen, it can still be accessed by scrolling).
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2019-03-15 Imroves Wheels view layout (not complete yet)
    The encoder part is currently organized in nested StackPanels in such a way which makes it difficult to make changes to the layout.
    TODO comment has been added to try and replace with RelativePanel.
    We will wait with those changes until the Encoder class has been modified (to allow for a second encoder on the right hand side).
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2019-03-18 Removes speed reduction from ExampleLogic L1b
    This was removed due to there is now a safety function coded into the Arduino which will automaticalle reduce speed if it gets too close to an obstruction.
    Doing this also in the control logic then caused the car to end up driving very slowly.
    Also increases distance from obstruction in front of car before it rotates away from obstruction from 0.2 meter to 0.5 meter.
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2019-03-19 Fixes encoder time wraparound from simulator
    Would not display higher that 999ms (would wrap arround).
    Changes so that it will display total miliseconds (e.g. can show 1543ms etc.).
2019-03-19 Fixes issue when navigating away from wheel page
    If navigating away from the wheel page, without first having turned on ApplyWheelSpeedContinously, the program would lock (due to _periodicRaisePropertyChangedToken.Cancel(); in OnNavigatingFrom would cause a null exception).
    Adds ?. operator to prevent Cancellatino if token is not initialized.
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2019-03-22 Changes Encoders CollectionInterval to int
    This commit fixes the issue where if the user entered a number into the seconds field in the textbox, it would be ignored (previously it only looked at the millisecond part, which at max could be 999).
    Also limits the smallest value the user is allowed to set (againts a private constant).
2019-03-22 Fixes 'multiple Encoder Collectors running' bug
    It was possible to accidentaly have several collectors running simultaniously.
    This would occur if the CollectContinously bool was set to false, and then true again before the while loop had completed (i.e. before Thread.Sleep() completed).
    This would in turn cause the collectoins to occure too frequently.
    This fix introduces a cancellation token and a cancellable await Task.Delay() instead of Thread.Sleep().
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2019-03-22 Additional fix to multiple collectors running bug
    Sometimes when togle switch was pushed, the setter was accessed two times in quick succession with the same value (true) causing the collector to start twice.
    This same issue could also be caused if property were to be set from ControlLogic to the same value it allready was.
    This issue has now been fixed.
    (setting collectorTokenSource to null, and checking in the if-block is probably not neccesary, but was added as extra safety measure).
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2019-03-22 Changes properties to private and AvgVel from calc
    Sets propoerty setters to private since there is no reason for them to change from outside the class.
    Therefore a method is also created to reset TotalDistance inside the Encoder class, so that Encoders class doesn't have to call the properties for Left and Right encoder directly.
    Average velocity property has been changed from caluclated to one that gets set when new data is received.
    (Also adds a lock arround the code for calculation)
    The reasons for this are:
    - The only time it is nessecary to calculate the distance is after new data is received.
    - If it were calculated on request (which could happen from a different thread) there is a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
2019-03-23 Removes incorrect BUG comment for Lidar MedianCalc
    The code sorts by distance (Values list is a list of distances, not points), and then returns the middle element.
    Note that it does not average the middle element in the case of even number of elements.
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2019-03-23 Fixes BUG when lidar distance spanned zero
    This commit fixes bug where GetDistances/HorizontalPoints in range would not return any values WHEN fromAngle-toAngle was spanning zero AND there were no measured values on the left hand side of zero.
2019-03-27 Inproves Lidar range selection for point calc.
    Replaces textbox input with sliders, for selecting the angles to calculate horizontal points for.
    Also adds a ToggleSwitch to start/stop point calculation.
    This commit also puts the Direction calculation and Point calculation (when activated by the sliders) into tasks (runs on threadpool instead of UI thread).
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2019-03-27 Replaces Lidar-settings TextBoxes with ComboBoxes
    This was done to make them easier to use on the vehicles touch screen.
    TODO/BUG reminder has been added in comments to look into making them editable (1809) in a robust manner.
    The LidarDistance MinRange and MaxRange has been changed from Float to Double, since x:Single did not seem to be available in the XAML for our UWP app (despite the .NET Framework having it https://docs.microsoft.com/en-us/dotnet/framework/xaml-services/built-in-types-for-common-xaml-language-primitives ).
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2019-03-29 Adds control logic using LIDAR and Ultrasound
    Tested (with safety function disabled), and has been driving far through the corridors without issues.
2019-04-01 Changes direction-to-turn logic and increases limit fwd
    Note that using 0.3f was working fine when testing (without safety function active).
    But to avoid interference by safety function once it gets fixed, the distance was increased to 0.5.
    This had the side effect of the ultrasound now detecting the door-thresholds, and therefore no longer able to pass over them.
    We are considering angeling the sensors upwards slightly to avoid this.
2019-04-02 Minor improvements to Wheel View speed-sliders
    Puts stepfrequency of 5 for sliders. Also stop button no longer resets sliders (unless auto-apply wheel speed is on).
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2019-04-05 Replaces Vehicle Sprite texture (Prototype2)
    Replaces red-car texture with photo of prototype 2.
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2019-04-10 Replaces textbox with ComboBox on WheelsPage
    Also:
    - Adds some space between buttons (Margins).
    - Standerdizes brackets for units to [ ].
2019-04-10 Replaces textbox with ComboBox on UltrasonicPage
    This includes changing the variable holding the PermissableDistanceAge from a TimeSpan to an int.
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2019-04-10 Changes EquipmentOverview and ExampleLogic icon
    - Changes order of Example Logic and Student Logic, so that Example Logic appears first in the side menu.
    - Removes old TODO comments (there is no longer any plan to create separate page for encoder, and icons have allready been added).
    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
2019-04-10 Improves LidarPage with new collection time
    Adds stopwatch for collection time and interpretation time in LidarDistance class.
    On LidarPage:
    - Replaces the DateTime for LastUpdate with the new times from stopwatches.
    - Moves the time fields to the top.
    - Adds spaceing between 'Remove from active' and 'Set as default' button.
    - Increased fontsize of the info text when 'Display data' is off (to the same size as that for 'Run Collector' off info). And made information text for when 'Run Collector' is off to bold, so that it still will be more visible.
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2019-04-12 Adds dynamic color to StudentLogic button
    It turns green when a student logic is running, and gets a red frame if it has an unacnowledged error.
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2019-04-14 Improves error message display for Control Logics
    User can now toggle between simple error message and detailed message (including stack trace).
    It has been implemented for both StudentLogic and ExampleLogic.
    TODO comment has also been added to remind to extract error properties/methods out to separate separate class, and to implement the new display layout to the other models.
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2019-04-14 Replaces Settings StackPanel with Grid
    Replaces common stackpanel for all elements on page with grid columns and rows to increase placement flexibility.
    (This was done in preperations for buttons that will be added to switch on/off experimental/other functions like the Android application).
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2019-04-16 Creates Error class to hold error message etc.
    This was done since most of the models and the two control logic bases all requires these fields/methods.
    Extracting this out to a separate class which gets instantiated in each of those models instead will keep the code DRY and the other classes cleaner.
    It also makes it easier if we wish to add logging at a later stage, since this then can be easily placed in the Error class.
2019-04-16 Improves error-message display/code for Ultrasound
    Replaces error-related fields with Error class in the Ultrasonic Model.
    Also improves the displaying of error message in the view/page.
    This new display is the same as the one developed for the ExampleLogics, with red text and buttons for toggling details or clearing error.
    Also added a TODO reminder to try and find a good solution for scrolling text to prevent data being pushed off screen if the exception message is too long.
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2019-05-06 Exits client loop when null-string is received
    Reads received request in SocketServer's while-loop and checks if null.
    If the string received is null, it means the client closed the connection.
    Also removes the no longer needed "Exit" request and other code connected with communicating a client exit.
    [ParseServerRequest.java]
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
